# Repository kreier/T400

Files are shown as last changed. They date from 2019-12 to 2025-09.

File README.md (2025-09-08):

# T400





Robot car with WiFi, programmed and controlled by MicroPython. The OLED screen gives information about status, connection and WiFi network to connect to (AP mode).

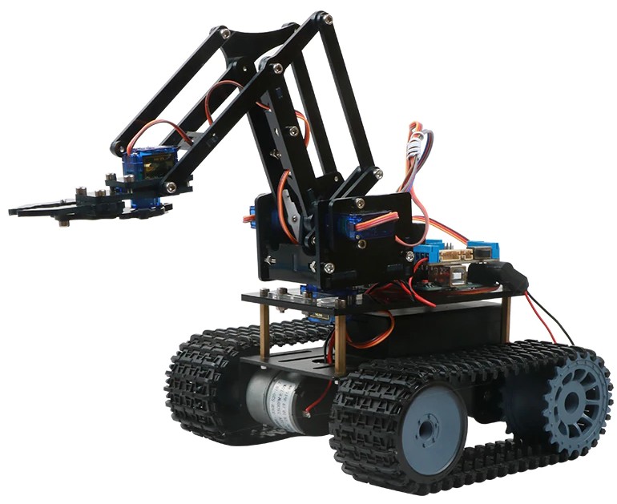
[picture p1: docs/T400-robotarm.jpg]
T400

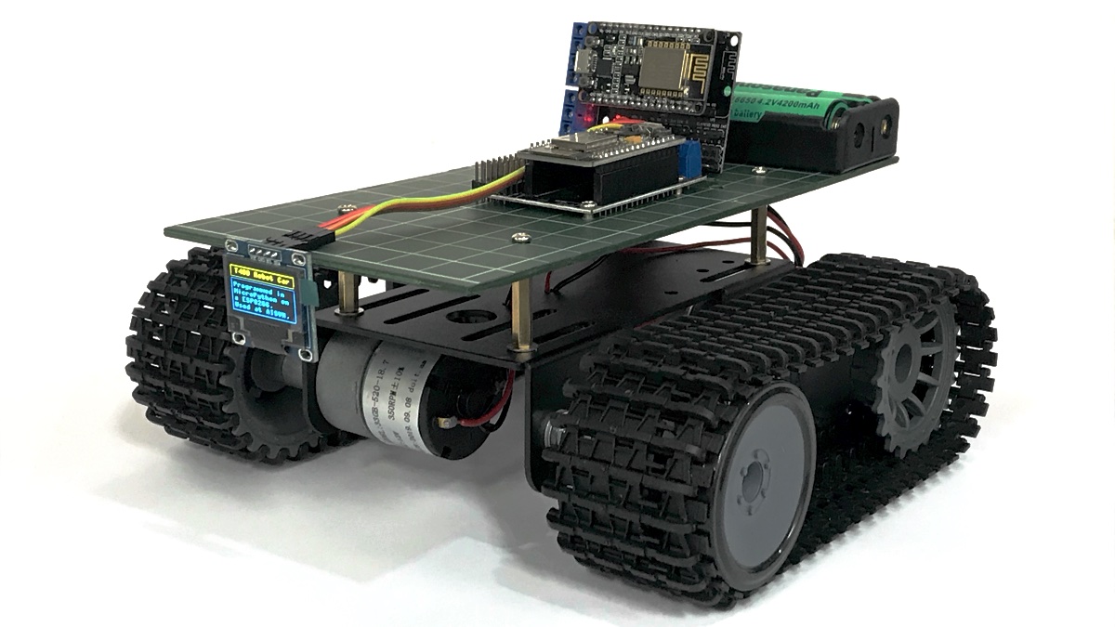
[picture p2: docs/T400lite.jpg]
T400 lite


## Project

This car was build during ASA session III in 2019/2020 at the AISVN. In 11 weeks from February 24th to May 22nd we successfully created 8 robot cars. Here are some pictures of the finished products:

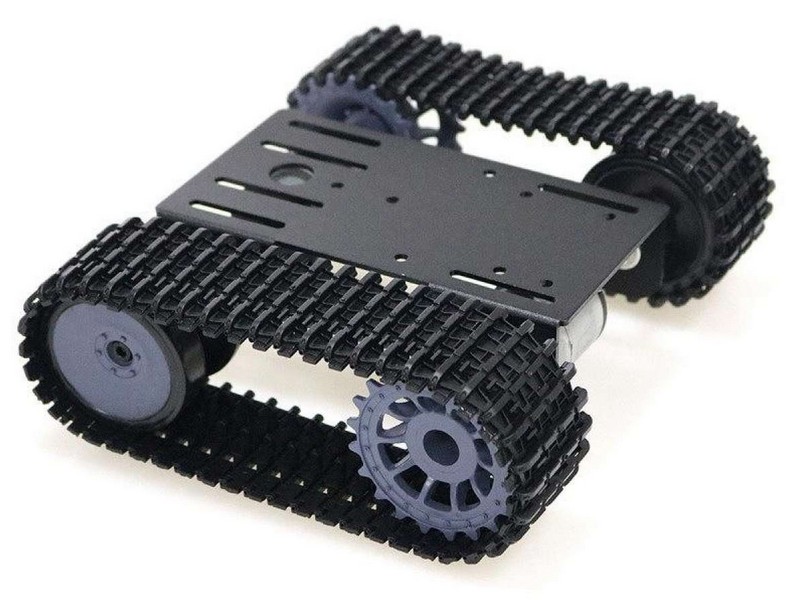
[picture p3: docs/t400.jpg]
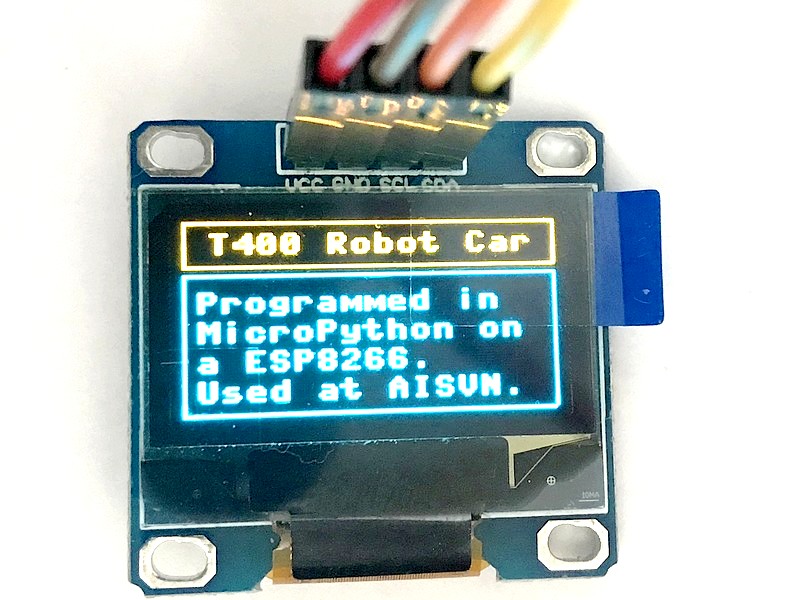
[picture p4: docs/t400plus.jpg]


### Key features

Over the time of 3 months the students will reach different stages of their project, but here are some key features:

- Central unit is a ESP8266 with 32 kByte RAM and 4 GByte Flash memory, running at 160 MHz.
- The programming language is [MicroPython](https://en.wikipedia.org/wiki/MicroPython) with an interactive prompt [REPL](https://en.wikipedia.org/wiki/Read%E2%80%93eval%E2%80%93print_loop).
- The control unit is powered by a standard 5V powerbank.
- The drive unit is a caterpillar base with two 12V motors.
- The robot car can be controlled via WiFi.
- An OLED display 128x64 (ssd1306) gives status updates.

## Materials

The materials used for this project were ordered at [IC ĐÂY RỒI](https://icdayroi.com/), [thegioiic.com](https://thegioiic.com/) and [lazada.vn](https://www.lazada.vn/#). Here is a list of materials:

| Nr | Name | Amount | Unit Price | Sum | Supplier |
|:--:|---|:---:|---:|---:|:---:|
|  1 |ESP8266 NodeMCU | 1 | 83000 VND| 83000 VND| [link thegioiic](https://thegioiic.com/products/lua-esp8266-cp2102-nodemcu-wifi-module) |
| 2 |Motor Shield L293D | 1 | 30000 VND| 30000 VND| [link thegioiic](https://thegioiic.com/products/esp12e-lua-l293d-de-ra-chan-wifi-esp8266-nodemcu) |
| 3 |OLED display 126x64 I2C | 1 | 79000 VND| 79000 VND| [link thegioiic](https://thegioiic.com/products/lcd-oled-0-96inch-128x64-iic-4pin-chu-trang) |
| 4 |Wires DuPont MF and FF | 20 | 300 VND| 6000 VND| [link thegioiic](https://thegioiic.com/products/day-be-cai-cai-dai-15cm) |
| 5 |Robot caterpillar 12V unit | 1 | 483000 VND| 483000 VND| [link lazada.vn](https://www.lazada.vn/products/smart-tank-car-chassis-tracked-caterpillar-crawler-robot-platform-with-dual-dc-12v-motor-for-diy-for-arduino-t101-ptp101-i402162026-s6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) |
| 6 |Powerbank 10000 mAh 2 USB | 1 | 249000 VND| 249000 VND| [link nguyenkim](https://www.nguyenkim.com/pin-sac-du-phong-mili-power-shine-ii-hb-m90bk.html) |
| 7 |DC step-up converter 5V 12V | 1 | 23000 VND| 23000 VND| [link thegioiic](https://thegioiic.com/products/xl6009-mach-tang-ap-4a) |
| 8 |Robot 4DOF kit | 1 | 246000 VND| 246000 VND| [link lazada.vn](https://www.lazada.vn/products/4-dof-acrylic-chua-lap-rap-diy-canh-tay-robot-diy-bo-cho-arduino-may-lam-ho-tro-hoc-tap-sg90-servo-i267650656-s391094259.html) |
| 9 |Servo SG90 | 5 | 29000 VND| 145000 VND| [link icdayroi](https://icdayroi.com/servo-sg90) |
| 10 |Ultrasonic Module US-100 3.3V | 1 | 59000 VND| 59000 VND| [link thegioiic](https://thegioiic.com/products/us-100-module-cam-bien-sieu-am) |
| 11 |I2C servo controller PCA9685 | 1 | 49000 VND| 49000 VND| [link thegioiic](https://thegioiic.com/products/pca9685-dieu-khien-dong-co-servo-12bit-pwm-6-kenh) |
| 12 |USB male connector Type A | 2 | 1800 VND| 3600 VND| [link thegioiic](https://thegioiic.com/products/cong-usb2-0-typea-4pin-dau-duc-han-day) |
| 13 |Buzzer 3.3 Volt | 1 | 3000 VND| 3000 VND| [link thegioiic](https://thegioiic.com/products/module-coi-buzzer-3-3v-5v) |
| 14 |Screw M3 8mm | 8 | 550 VND| 4400 VND| [link thegioiic](https://thegioiic.com/products/vit-pm-m3-x-8mm) |
| 15 |HEX-M3 spacer 15mm | 4 | 1000 VND| 4000 VND| [link thegioiic](https://thegioiic.com/products/tru-dong-hex-m3-cai-cai-dai-15mm) |
|  | |  |  VND| 1467000 VND|  |

## Pin layout

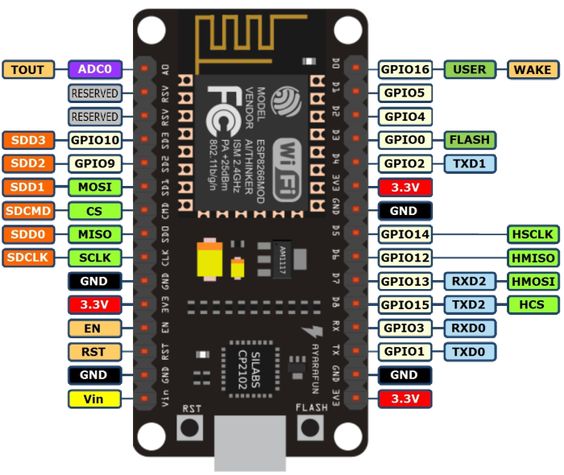
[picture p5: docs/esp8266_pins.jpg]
Pin esp8266


## Code

This is an example of the MicroPython code we are going to use:

``` py
from machine import Pin, I2C
import ssd1306

# ESP32 Pin assignment 
# i2c = I2C(1, scl=Pin(22), sda=Pin(21))

# ESP8266 Pin assignment
i2c = I2C(scl=Pin(12), sda=Pin(14))

oled_width = 128
oled_height = 64
oled = ssd1306.SSD1306_I2C(oled_width, oled_height, i2c)

# draw some boxes

for x in range(0, 127): # horizontal lines
  oled.pixel(x, 0, 1)
  oled.pixel(x, 15, 1)
  oled.pixel(x, 16, 1)
  oled.pixel(x, 63, 1)
  
for y in range(0, 63): # vertical lines
  oled.pixel(0, y, 1)
  oled.pixel(127, y, 1)

oled.text('T400 Robot Car', 8, 4)
oled.text('Programmed in', 4, 22)
oled.text('MicroPython on', 4, 32)
oled.text('a ESP8266.', 4, 42)
oled.text('Used at AISVN.', 4, 52)
  
oled.show()
```

## I2C connector

`2020/07/09`

Following the inspiration of SparkFun with their [QWIIC](https://www.sparkfun.com/qwiic#products) connector I tried to replicate the pin order. But instead of SMD 1.0 mm connector I just use the regular 2.54mm raster with XH connector on the board and respective 4 pin connector wire.

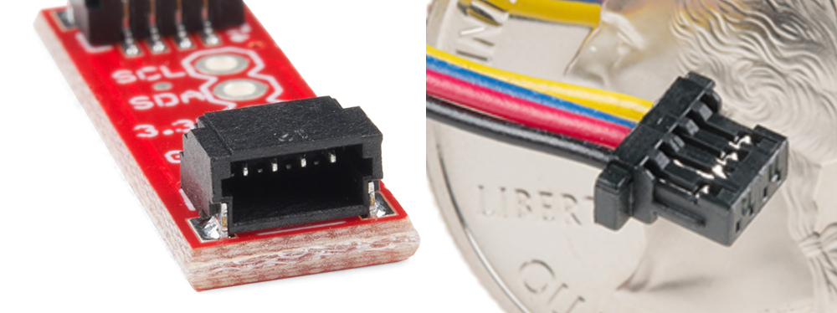
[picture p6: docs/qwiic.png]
QWIIC system


Following the same order the pins are assigned:
1. black - GND
2. red - 3.3 V
3. blue - SDA
4. yellow - SCL

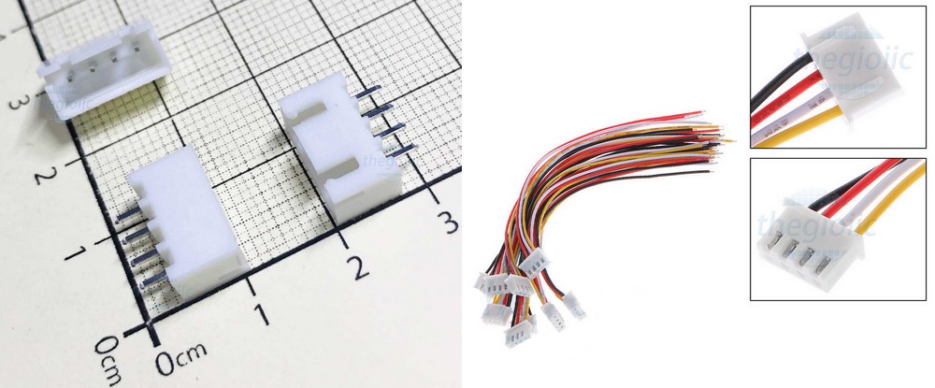
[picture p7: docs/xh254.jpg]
XH 2.54 connector


The order does not match several OLED displays, but the ZS-042 rtc clock, the 1602 display adapter and many more.

`2020/11/27`

With the new [T-Display](https://kreier.github.io/t-display/) project I included the I2C connector as well. The pins look like this:

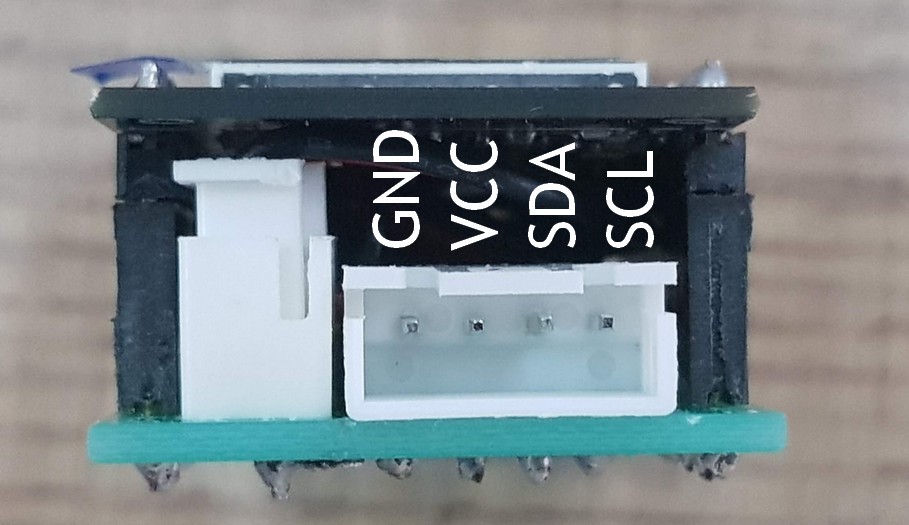
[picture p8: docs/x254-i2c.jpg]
I2C on T-Display


At the ESP32 SCL (SCK) is on GPIO 22 and SDA (SDI) is on GPIO 21.

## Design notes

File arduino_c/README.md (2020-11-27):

# Programming in C with the Arduino IDE

As a parallel development we have some code for the esp8266 on the motorshield board written in C. It helps troubleshooting behaviour and usability of pins, combinations etc.

The board uses the pin D1 to D4 to control tle L293DD motor bridge. The I2C is usually booked on these pins, they have to be remapped therefore.

## I2C Display 1602

It works only with D5 and D6. D7 and D8 throw errors when unconnected to a I2C bus and stop the program when connected. Same is for SD2 and SD3 (GPIO9 and GPIO10). Connection is

| PIN | GPIO | I2C |
|-----|---|-----|
| D6  | 12 | SDA |
| D5  | 14 | SCL |

``` c
#include <LiquidCrystal_I2C.h>
#include <Wire.h>

LiquidCrystal_I2C lcd(0x27, 16, 2);

void setup(){        // usually I2C on D1 and D2, but used for motor driver
  Wire.begin(12,14); // I2C on D6/GPIO12/SDA and D5/GPIO14/SCL
  lcd.init();
  lcd.backlight();
  pinMode(16, OUTPUT);
}

void loop(){
  for(int i = 0; i < 2; i++){
    lcd.setCursor(0, i);
    lcd.print("Hello, World!");
    digitalWrite(16, i);
    delay(500);
    lcd.clear();
  }
}
```
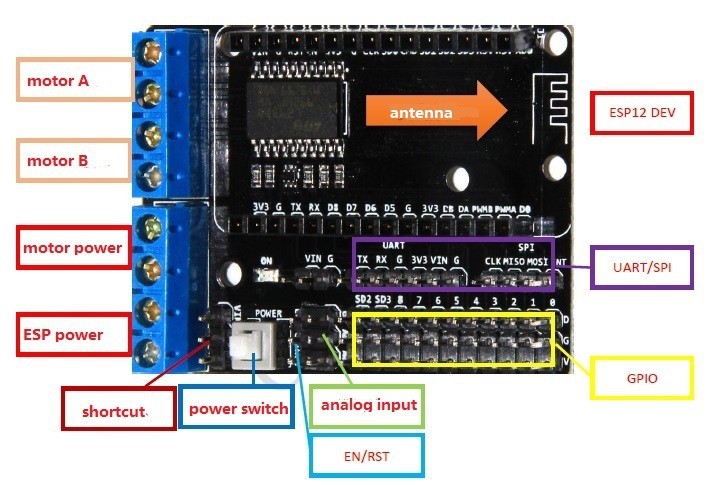
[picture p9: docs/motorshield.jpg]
motorshield


## Remote controlled robot

A great project has been done by [Vincent Lacour](https://github.com/lacour-vincent) to create a remote controlled robot car with an ESP8266. He wrote an app to control the robot using WiFi, let's later update the code to directly control the robot in a browser.

Link to his project (November 2019):

- Code https://github.com/lacour-vincent/wifi-car-esp8266
- Android app: https://play.google.com/store/apps/details?id=com.lacour.vincent.wificaresp8266
- iOS app: not yet there

Other notable projects:

With Remoteme: https://www.hackster.io/WolfxPac/wifi-controlled-robot-using-esp8266-8756b7 2019/01/01

With Blynk: https://www.instructables.com/id/Wifi-Controlled-Robot-Car-Using-Nodemcu-and-Blynk/ 2019/07/05

Simple https://www.hackster.io/alankrantas/simple-nodemcu-wifi-controlled-car-esp8266-c5491e 2019/08/19

## OLED display at I2C

For slightly more money one can get an OLED display for the I2C bus, which has a better resolution than the 1602 display, supports graphics and is smaller in size - perfect for a small robot. To deceide if I should go for 0.96" or 1.3" I ordered both and compared the output of both displays, since both have the same resolution:

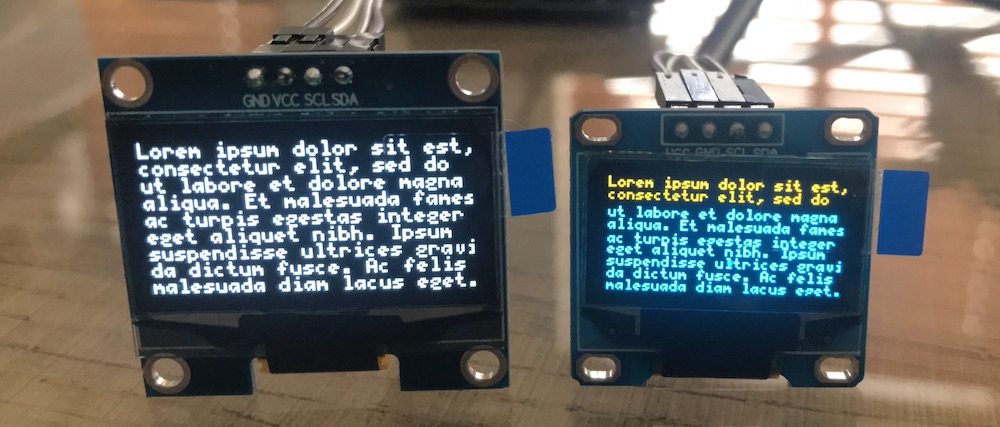
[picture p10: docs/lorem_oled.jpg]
SH1106 and SSD1306


Clearly the larger SH1106 display is to prefer compared to the smaller SSD1306 variant in two colors.

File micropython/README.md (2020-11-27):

# Micropython on the ESP8266

## Install Micropython

Instructions are found at [micropython.org](https://docs.micropython.org/en/latest/esp8266/tutorial/intro.html). For example you can check the size of your flash with `esptool.exe --port COM5 --chip auto flash_id`. Use the firmware found at [the download page of micropython.org](http://micropython.org/download#esp8266) and flash the new firmware with

```
esptool.py --port COM5 --baud 460800 write_flash --flash_size=detect 0 esp8266-20200103-v1.12.bin
```

Now you can connect to your esp8266 using [uPyCraft](http://docs.dfrobot.com/upycraft/) or [Thonny](https://thonny.org/). For the first one you might want to install [SourceCodePro.ttf](https://github.com/kreier/python2018/raw/master/micropython/SourceCodePro.ttf) for all users to avoid the error message.

## Using the OLED display

The OLED display is connected via I2C and the pins are remaped to GPIO 14 (SDA) and GPIO 12 (SCL) because the standard pins are used by the motorshield. In 0.96" and 1.3" it looks like this:

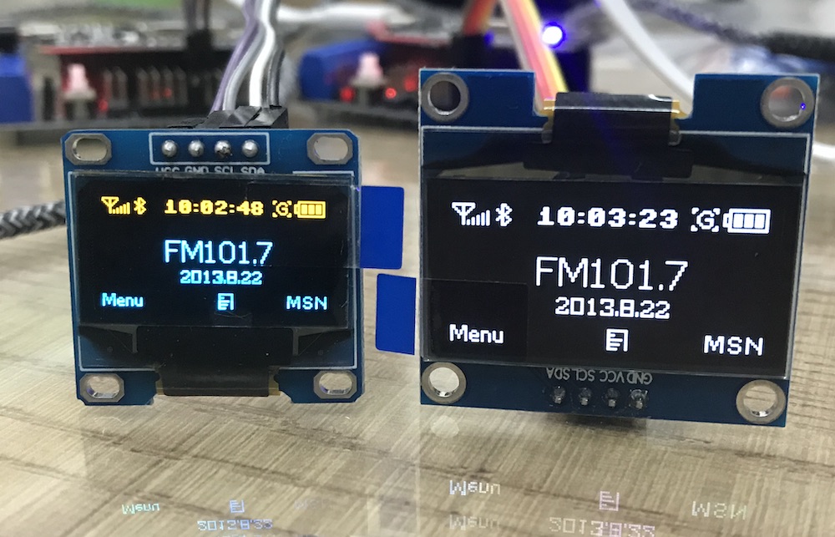
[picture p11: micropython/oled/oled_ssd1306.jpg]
small vs big


## Logfile

`2020/11/27`

Too many external components. The T-Display has a TFT display included, with color and higher resolution and with ESP32 and battery controller ...

`2019/12/05`

Why Micropython? Because we teach python at school. It is used by data scientists. We use it in Jupyter notebooks. It is easier to learn than Arduino C.

And it has REPL - Read Evaluate Print. You get an immediate response. After flashing micropython v1.11 to my NodeMCU in five minutes the first blink from the commandline was working. Flipping pins without compiling and upload a program is GREAT!

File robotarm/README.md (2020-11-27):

# Robotarm

> [Link to robot arm for T400](MeArm/README.md)

The T400 should be equipped with a robot arm. Due to financial constrains we are going to use a $11 (246,000 VND) lasercut acryl 4 DOF arm with SG50 servos. The final robot should look like this:

T400 with robot arm

## 3D printed robot arm - EEZYbotARM MK1 and MK2

In 2015 and italian maker designed a printable [robot arm MK1](https://www.thingiverse.com/thing:1015238). It was very successfull and downloaded more than 120,000 times.

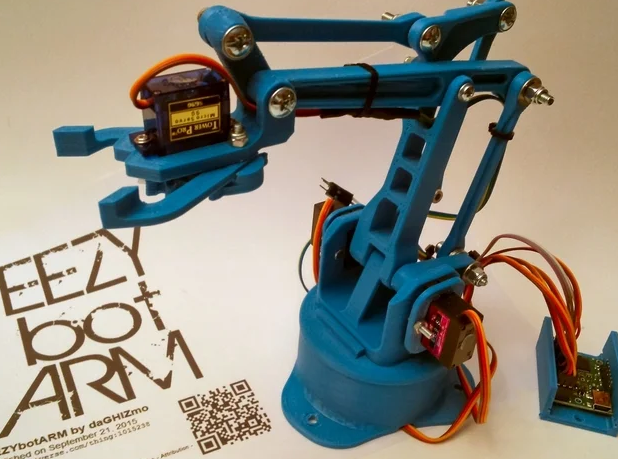
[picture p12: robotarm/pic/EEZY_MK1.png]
EEZYbotARM MK1


Soon he found it to be too small and [created the MK2](https://www.thingiverse.com/thing:1454048) in 2016. It is downloaded at [thingiverse](https://thingiverse.vom) some 110,000 times. You can get it printed in HCMC for example at [makerstore.vn](http://makerstore.vn) for 281,00 VND (MK1) or 525,000 VND (MK2). They have the screws and servos as well.

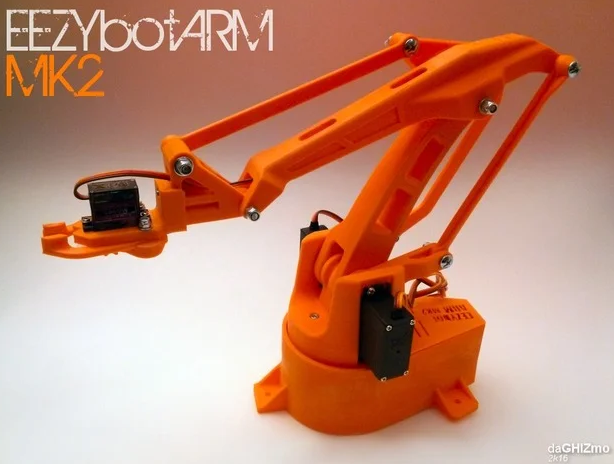
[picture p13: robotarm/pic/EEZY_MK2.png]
EEZYbotARM MK2


## Robot arm 6 DOF from China

At Aliexpress you can order the metal materials for a 6 DOF robot arm for $25. Equipped with 1Nm digital servos like MG996R the product is rather versatile. See it here in action:

`2020/01/12` The kit was just ordered. And we need the servos ...

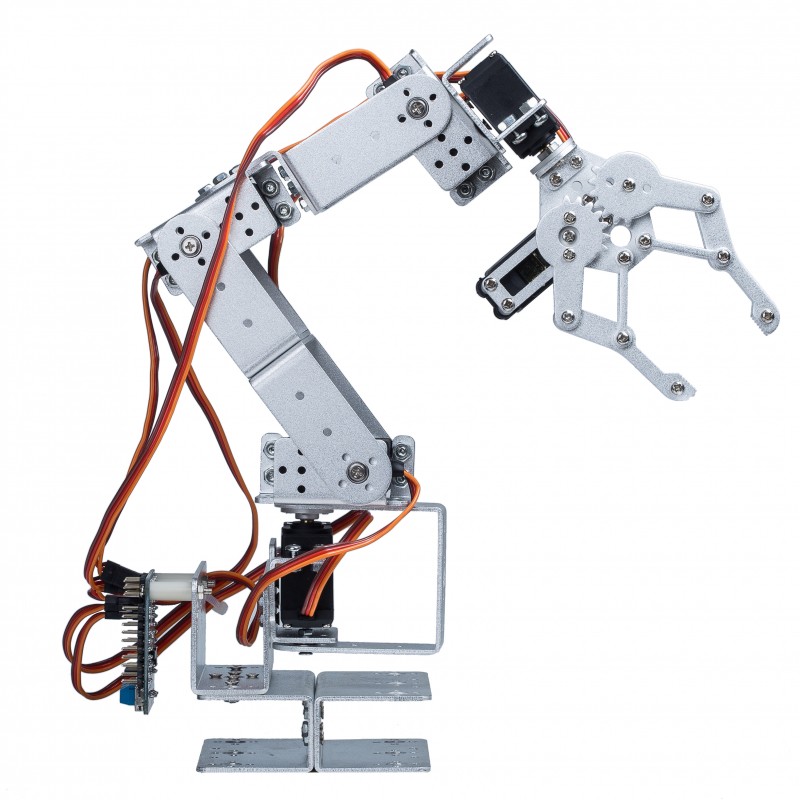
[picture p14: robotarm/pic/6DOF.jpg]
6 DOF


## Design a robot arm ourselves

Inspired by the relative stability of the digital servo driven robot arm and the design of the KUKA KR 3 AGILUS.

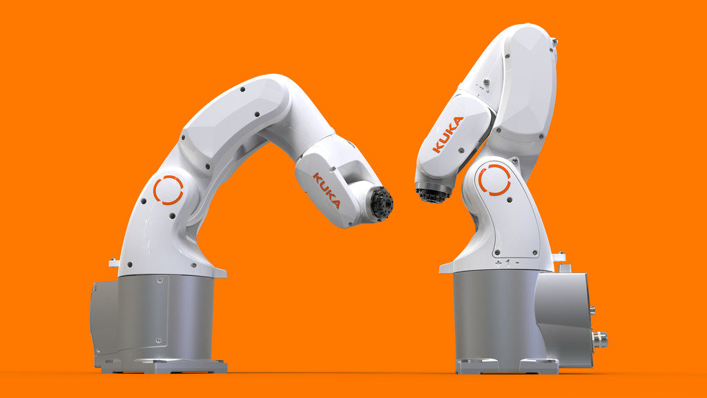
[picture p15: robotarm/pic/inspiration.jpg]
KUKA R3


## Stepper motors

One design with stepper motors is the [WE-R2.4 robot](https://www.thingiverse.com/thing:3327968) that was published in January 2019 by [LoboCNC](https://www.thingiverse.com/LoboCNC/about). Another user [John Lauer](https://github.com/chilipeppr) from [Chilipeppr](http://chilipeppr.com/arm) tried to build this arm and published a [first video](https://www.youtube.com/watch?v=tEbJV32GyYU) in February 2019. [Part 2](https://www.youtube.com/watch?v=RdmdFIhCo4M) from March 2019 had the controller software and hardware based on the ESP32 finishd. But there are several problems:

- Heat
- Homing
- Backlash
- Wiring
- Jogging
- Training

By September 2019 these where addressed and resolved or improved. See [Part 3 video](https://www.youtube.com/watch?v=4o3d7_WZ_DQ). Couldn't find a number for the produced torque or maximum rpm, though.

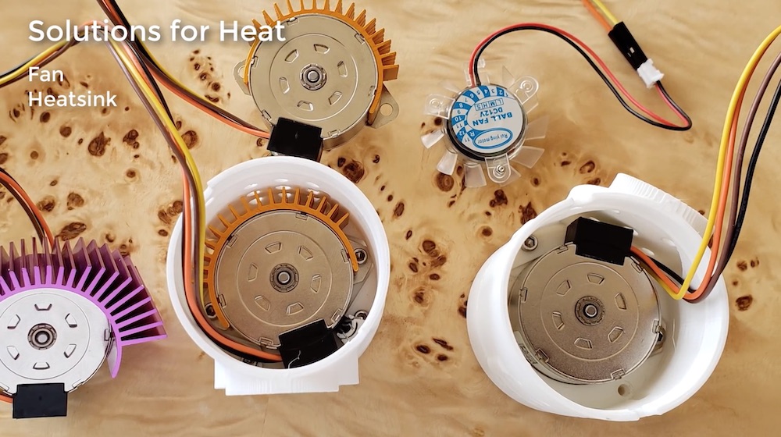
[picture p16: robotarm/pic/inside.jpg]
cooling

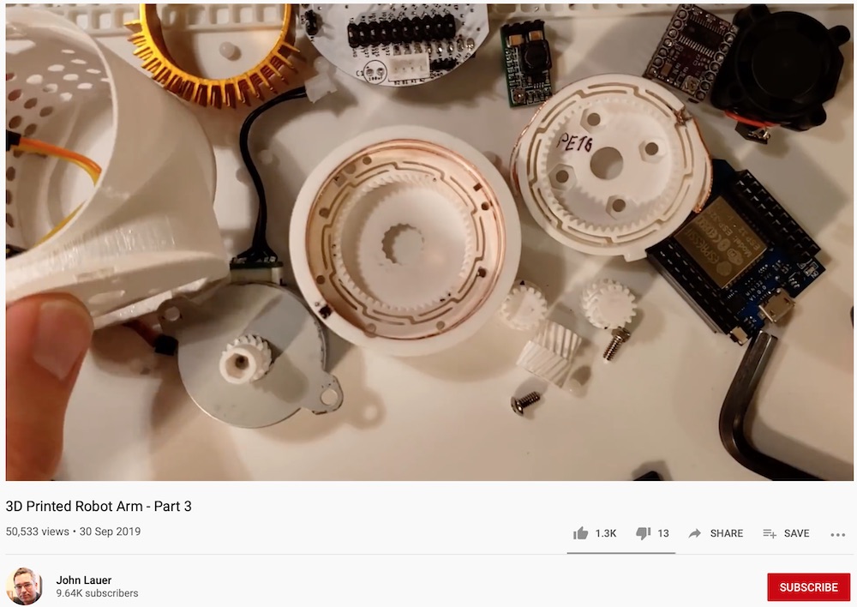
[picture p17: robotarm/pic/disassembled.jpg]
disassembled


## Mirobot - successful Kickstarter from September 2019, starting $295

Project [on Kickstarter](https://www.kickstarter.com/projects/mirobot/mirobot-6-axis-mini-industrial-robot-arm/description). Shipping started January 2020. Got more than $300.000. Later on [Indogogo](https://www.indiegogo.com/projects/mirobot-6-axis-desktop-robot-arm#/) as well. This is how it looks:

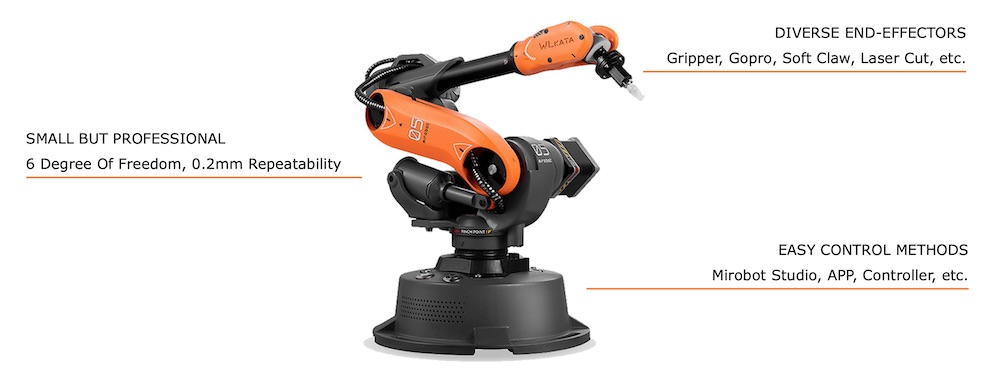
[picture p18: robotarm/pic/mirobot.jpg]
Mirobot


## GLUON by INNFOS - suspended on kickstarter

What [a promising project](https://www.kickstarter.com/projects/1383636492/the-smallest-servomotor-robotic-arm)! Fast and silent brushless actuators for $99 each (SCA QDD Lite-NE30-36) or an entire 4DOF for $519 or 6DOF robot arm for $899. But there might be some tentions with the investors, after funding from 612 backers for $519.848 in November 2019 (success in 30 seconds) the project was suspended by kickstarter in 2020. [Link to video](https://www.youtube.com/watch?v=-xzvWhRDGDU). Looked like this:

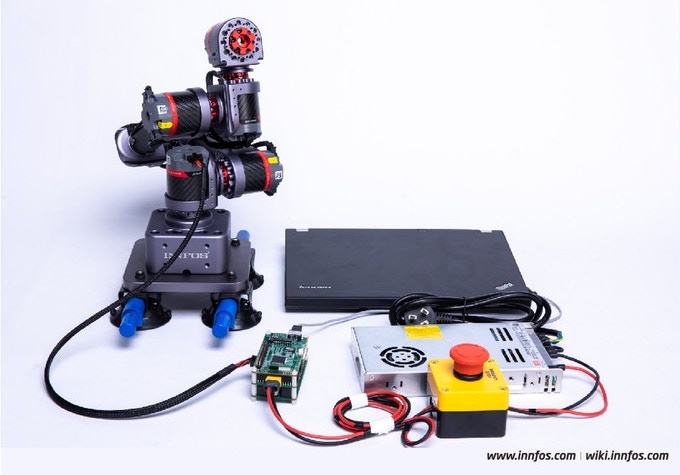
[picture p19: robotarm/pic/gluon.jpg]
INNFOS GLUON


## How to Mechatronics - back to simpler parts

While investigating I found another project that shares a lot of files and information and has a simple robot arm design with servos. It is [this project on howtomechatronics.com](https://howtomechatronics.com/projects/arduino-robot-arm-and-mecanum-wheels-platform-automatic-operation/) from [Dejan](https://howtomechatronics.com/author/howtom12_wp/). He made [a video about his project](https://youtu.be/LBNRGBY5zN8).

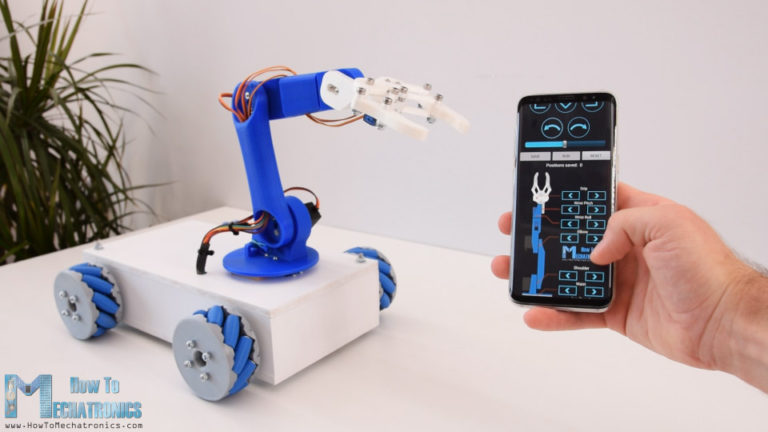
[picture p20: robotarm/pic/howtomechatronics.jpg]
Finished robot


He even created a Android App with MIT App invenbor to control his robot. We might use this for our T400. We don't have the stepper motors for our base as he does, but we might modifiy our code to fit the esp8266 instead of a Arduino Mega.

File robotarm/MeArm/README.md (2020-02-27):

# Robot arm at T400

Limited time and resources led to the decision to use the MeArm v3.0 for our T400 project during ASA3. The assembly should take 25 minutes and can be followed [in this video](https://youtu.be/sPdbs9b5udQ).

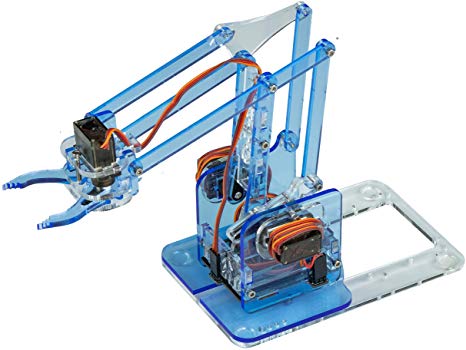
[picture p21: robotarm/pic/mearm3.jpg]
MeArm v3.0


The files are located in this folder and sourced from [here](https://www.thingiverse.com/thing:3420797/files) and [here](https://github.com/mimeindustries/MeArm). The modification is the removal of the text for the lasercutting and shortend of some corners to fit on the base of the robot.

## PCB

The files for the PCB are not provided, so they have to be recreated. This file should serve as inspiration, the rations are all given in the dxf file or can be measured there:

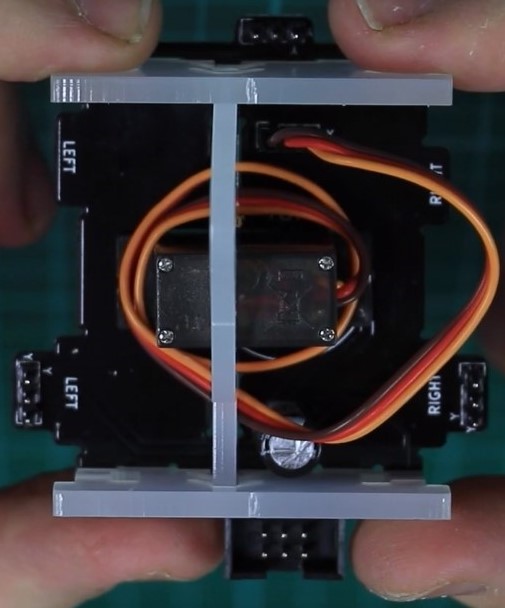
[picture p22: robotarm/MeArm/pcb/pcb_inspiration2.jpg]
PCB closeup


## Additional materials

Aside from the laser cut 3mm acrylic we need some M2.5 screws, no nuts! That's said [here in the video](https://youtu.be/sPdbs9b5udQ?t=455). So I count:

- 16x - M2.5 x 6mm
- 18x - M2.5 x 10mm
- 2x  - M2.5 x 16mm

I'll give it a try on January 31st, 2020.

## Licence

User phenoptix (Ben Gray from Nottingham) from Mime industries/MeArm published the following information on his website regarding the licence:

The hardware is released under [Creative Commons Share-alike 3.0](https://creativecommons.org/licenses/by-sa/3.0/).

All other code is open source so please feel free to do anything you want with it; you buy me a beer if you use this and we meet someday (Beerware license). Also this boiler plate is yoinked from Sparkfun with thanks. Images are CC-SA-NC soz, have the files and design but take your own pics ;)

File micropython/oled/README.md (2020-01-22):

# Text and graphics on 128x64 OLED i2c display

We use pin D5 (GPIO14) as SDA and D6 (GPIO12) as SCL for the i2c bus. The driver library 1306.py should be installed on the device. You can show any image 128x64 monochrome image. For example:

 

The code used is [splash3.py](splash3.py).

## Size 0.96 inch or 1.3 inch

For comparison I ordered the slightly larger display with 1.3 inch as well. It needs the different sh1106 driver, but has the same functions as the ssd1306. Text is easier to read. Here an image:

small vs big

## Convert images

I use the online [tool from majer.ch](http://www.majer.ch/lcd/adf_bitmap.php) and convert the code from ', 0x87' to '\x87' in the bytearray. Follow this instructions:

To create an image there is a description at [the micropython forum](https://forum.micropython.org/viewtopic.php?t=2974). In short deshipu says:

The buffer in the previous exampe is created by scanning the original image pixel-by-pixel and setting the bits of the bytes depending on whether they are supposed to be on or off. The alignment of the bytes is as follows (example of a 16x16 image, the digits signify the bits of each byte):

```
a7 b7 c7 d7 e7 f7 g7 h7 i7 j7 k7 l7 m7 n7 o7 p7
a6 b6 c6 d6 e6 f6 g6 h6 i6 j6 k6 l6 m6 n6 o6 p6
a5 b5 c5 d5 e5 f5 g5 h5 i5 j5 k5 l5 m5 n5 o5 p5
a4 b4 c4 d4 e4 f4 g4 h4 i4 j4 k4 l4 m4 n4 o4 p4
a3 b3 c3 d3 e3 f3 g3 h3 i3 j3 k3 l3 m3 n3 o3 p3
a2 b2 c2 d2 e2 f2 g2 h2 i2 j2 k2 l2 m2 n2 o2 p2
a1 b1 c1 d1 e1 f1 g1 h1 i1 j1 k1 l1 m1 n1 o1 p1
a0 b0 c0 d0 e0 f0 g0 h0 i0 j0 k0 l0 m0 n0 o0 p0
q7 r7 s7 t7 u7 v7 w7 x7 y7 z7 A7 B7 C7 D7 E7 F7
q6 r6 s6 t6 u6 v6 w6 x6 y6 z6 A6 B6 C6 D6 E6 F6
q5 r5 s5 t5 u5 v5 w5 x5 y5 z5 A5 B5 C5 D5 E5 F5
q4 r4 s4 t4 u4 v4 w4 x4 y4 z4 A4 B4 C4 D4 E4 F4
q3 r3 s3 t3 u3 v3 w3 x3 y3 z3 A3 B3 C3 D3 E3 F3
q2 r2 s2 t2 u2 v2 w2 x2 y2 z2 A2 B2 C2 D2 E2 F2
q1 r1 s1 t1 u1 v1 w1 x1 y1 z1 A1 B1 C1 D1 E1 F1
q0 r0 s0 t0 u0 v0 w0 x0 y0 z0 A0 B0 C0 D0 E0 F0
```

I used the following code to generate it:

``` py
import pygame

image = pygame.image.load("1bit-logo.png")
buffer = bytearray((image.get_height() // 8) * image.get_width())
i = 0
for y in range(image.get_height() // 8):
    for x in range(image.get_width()):
        byte = 0
        for bit in range(8):
            pixel = image.get_at((x, y * 8 + bit))
            if pixel[0] != 255:
                byte |= (1 << bit)
        buffer[i] = byte
        i += 1
print(repr(buffer))
```

After that _kamikaze_ added: `or you could use ImageMagick's convert and store it in file to save RAM`

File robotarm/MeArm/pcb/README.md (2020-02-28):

# PCB for MeArm3

The MeArm 3.0 uses a custom PCB to connect the 4 servos to a single flat cable with 6 pins and provide a physical base plate for the ground servo at the same time.

From the assemble video you can guess the shape:

PCB closeup

Since the shematics is not provided, it has to be recreated in EAGLE. Here my attempts: 

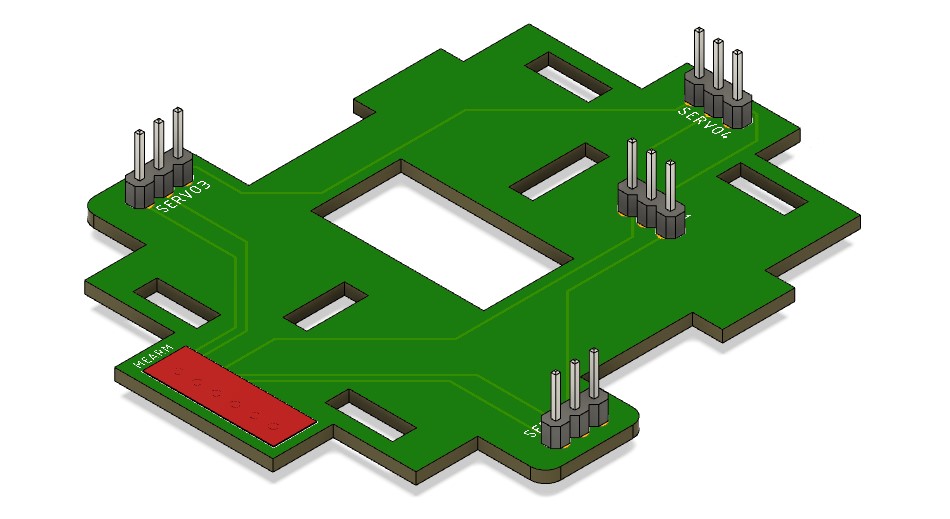
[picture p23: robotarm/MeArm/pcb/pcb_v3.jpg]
PCB v3


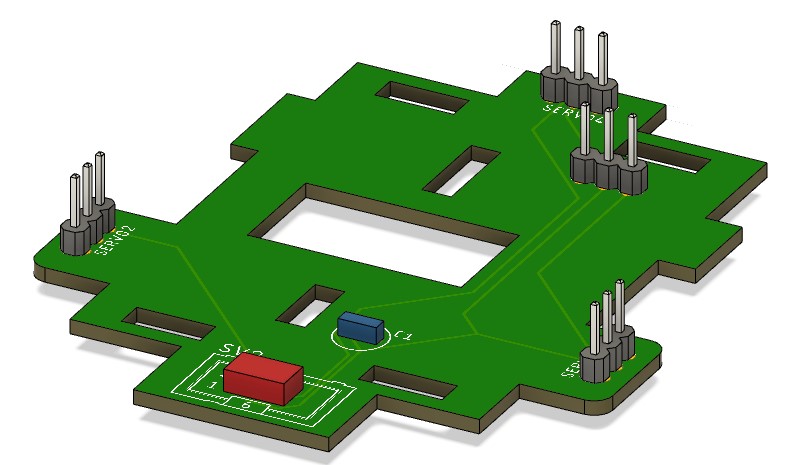
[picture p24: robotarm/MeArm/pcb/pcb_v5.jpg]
PCB v5


MeArm v3.0

The files are located in this folder and sourced from [here](https://www.thingiverse.com/thing:3420797/files) and [here](https://github.com/mimeindustries/MeArm). The modification is the removal of the text for the lasercutting and shortend of some corners to fit on the base of the robot.

## PCB

The files for the PCB are not provided, so they have to be recreated. This file should serve as inspiration, the rations are all given in the dxf file or can be measured there:

PCB closeup

## Additional materials

Aside from the laser cut 3mm acrylic we need some M2.5 screws, no nuts! That's said [here in the video](https://youtu.be/sPdbs9b5udQ?t=455). So I count:

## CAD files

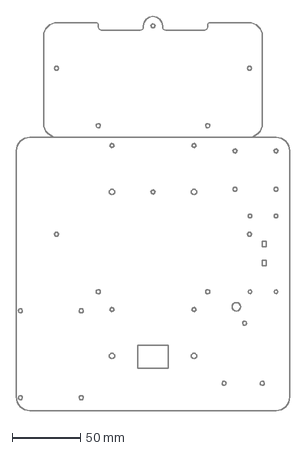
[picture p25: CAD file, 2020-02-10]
platform/T400platform.dxf
200.0 x 288.5 mm

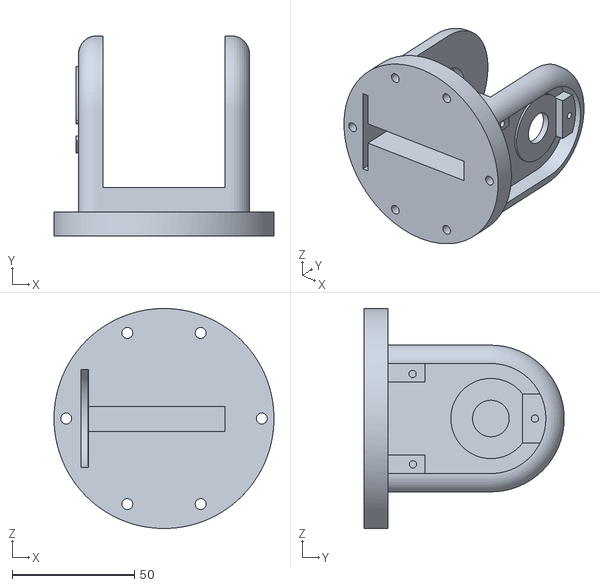
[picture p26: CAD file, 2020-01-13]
robotarm/base2.stl
90.0 x 82.0 x 90.0

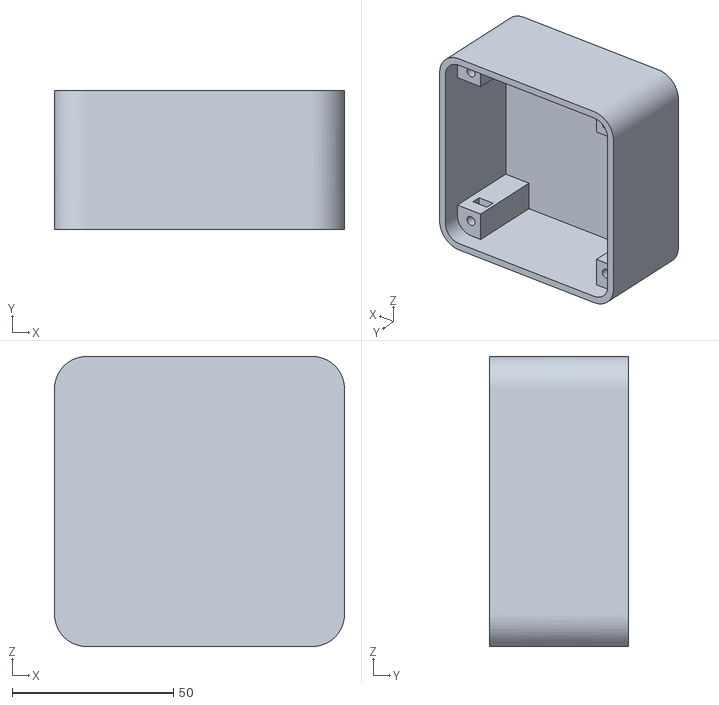
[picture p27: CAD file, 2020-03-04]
robotarm/loudspeaker/Box9.stl
90.0 x 43.0 x 90.0

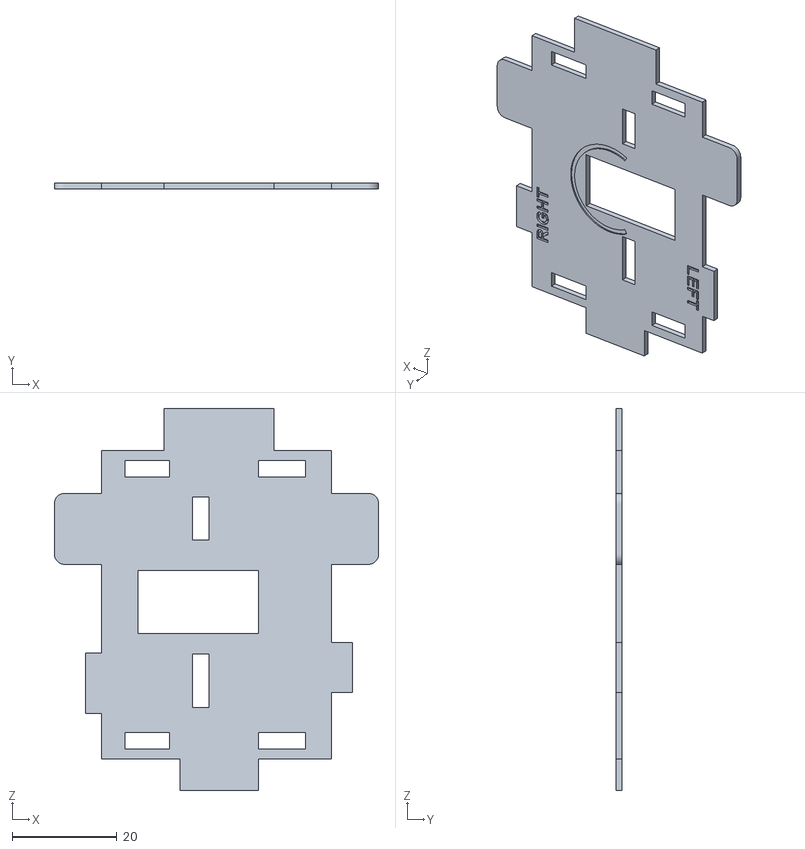
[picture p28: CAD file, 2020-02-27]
robotarm/MeArm/pcb/pcb_base v3.stl
62.0 x 1.20 x 73.0

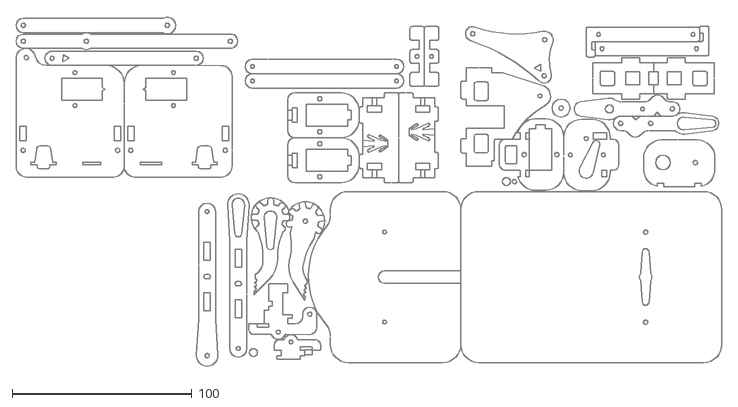
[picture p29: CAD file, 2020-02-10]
robotarm/MeArm/T400arm_plain.dxf
392.1 x 194.9

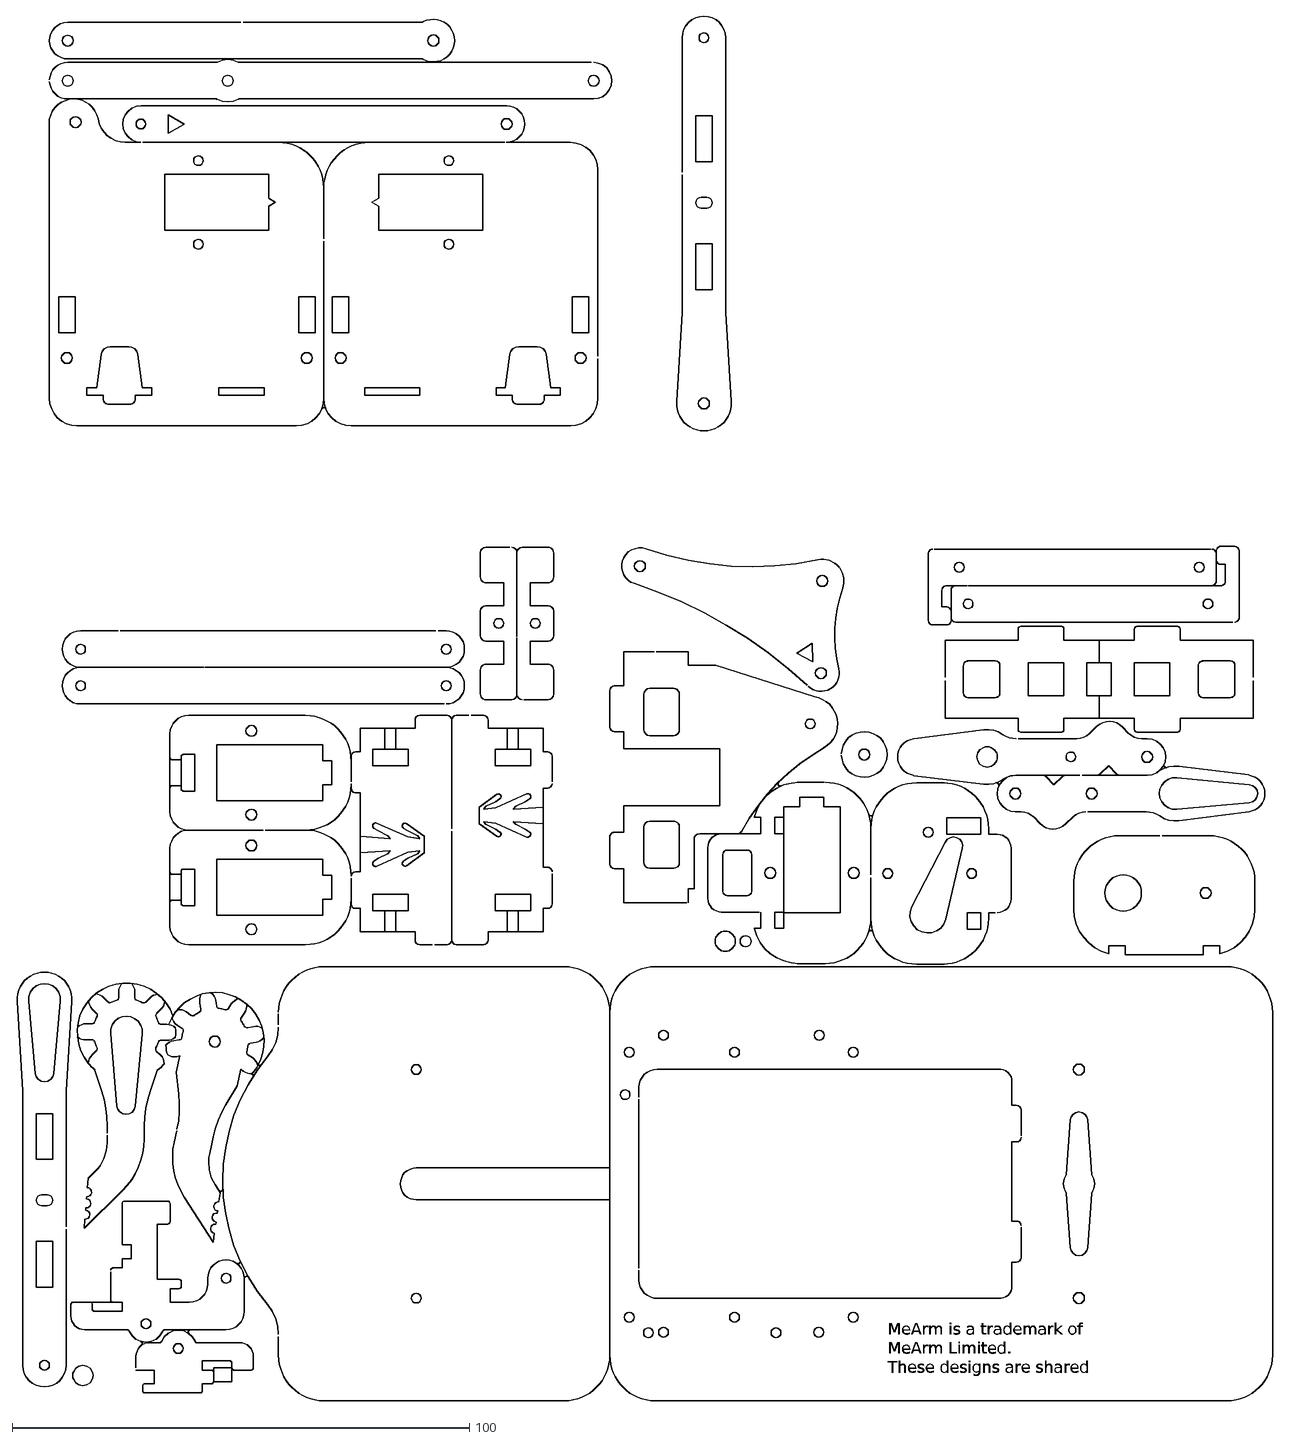
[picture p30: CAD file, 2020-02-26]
robotarm/MeArm/v3.0/MeArm3.0modified.dxf
MeArm is a trademark of
MeArm Limited.
These designs are shared

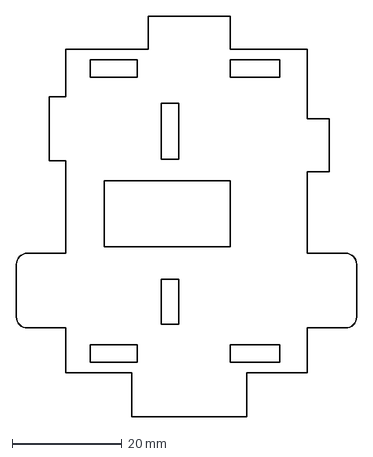
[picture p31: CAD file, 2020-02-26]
robotarm/MeArm/pcb/pcb_base_v4.dxf
62.0 x 73.0 mm

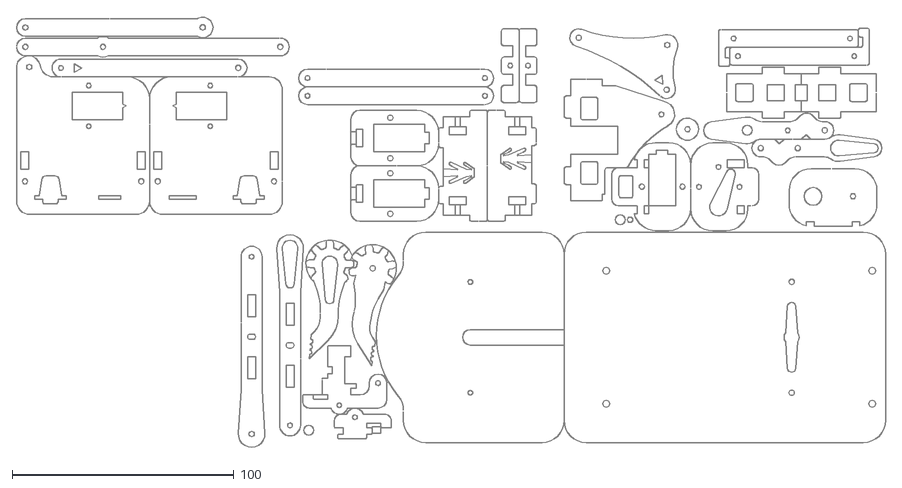
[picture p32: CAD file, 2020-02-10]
robotarm/MeArm/T400arm.dxf
392.1 x 194.9

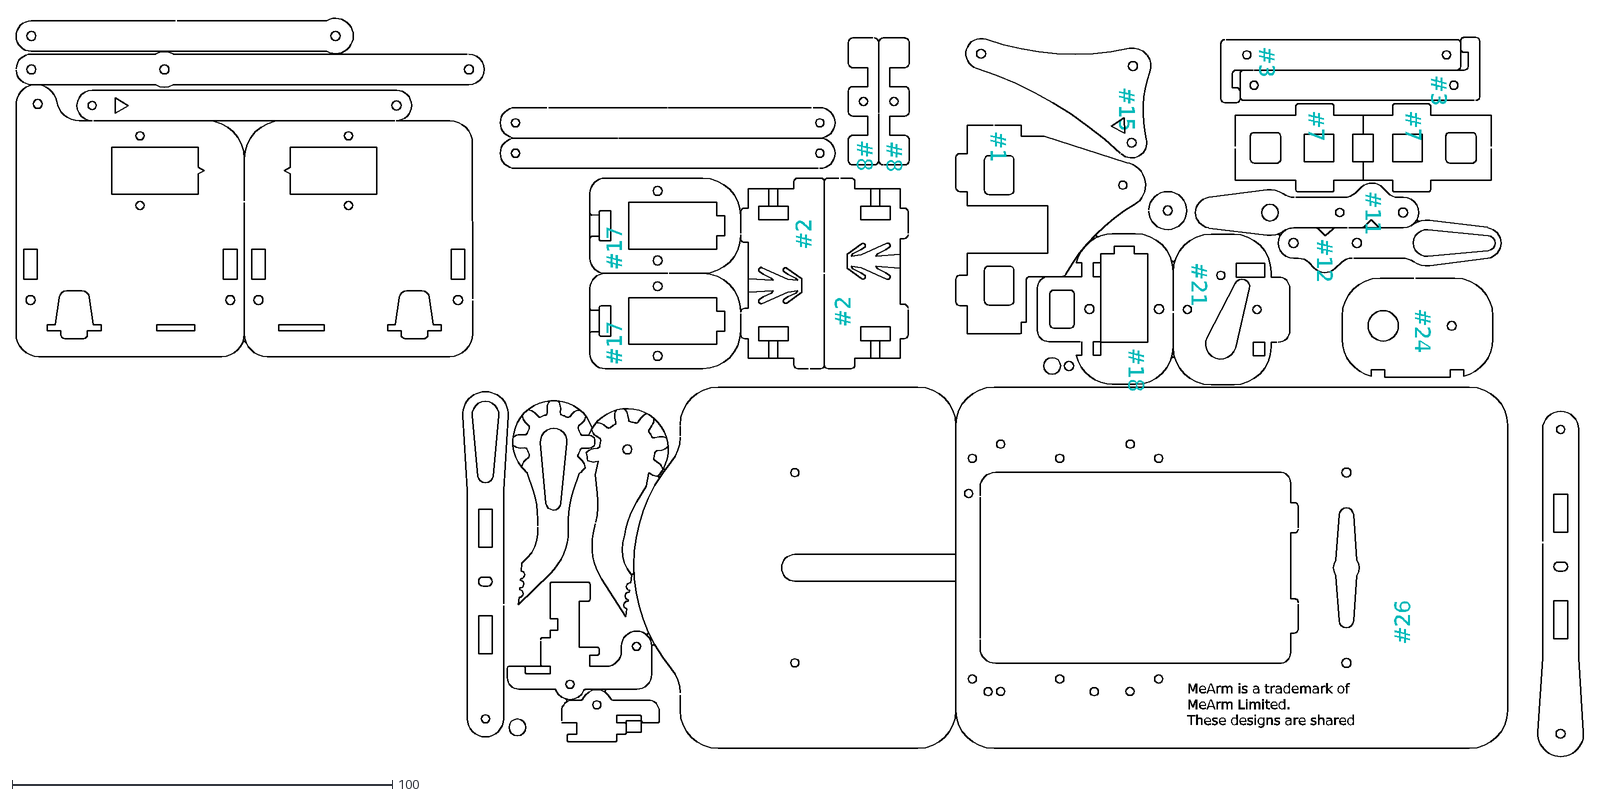
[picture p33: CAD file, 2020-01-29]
robotarm/MeArm/v3.0/MeArm3.0.dxf
#26
#1
#3
#7
#8
#11
#12
#15
#18
#21
#24
#2
#17
MeArm is a trademark of
MeArm Limited.
These designs are shared

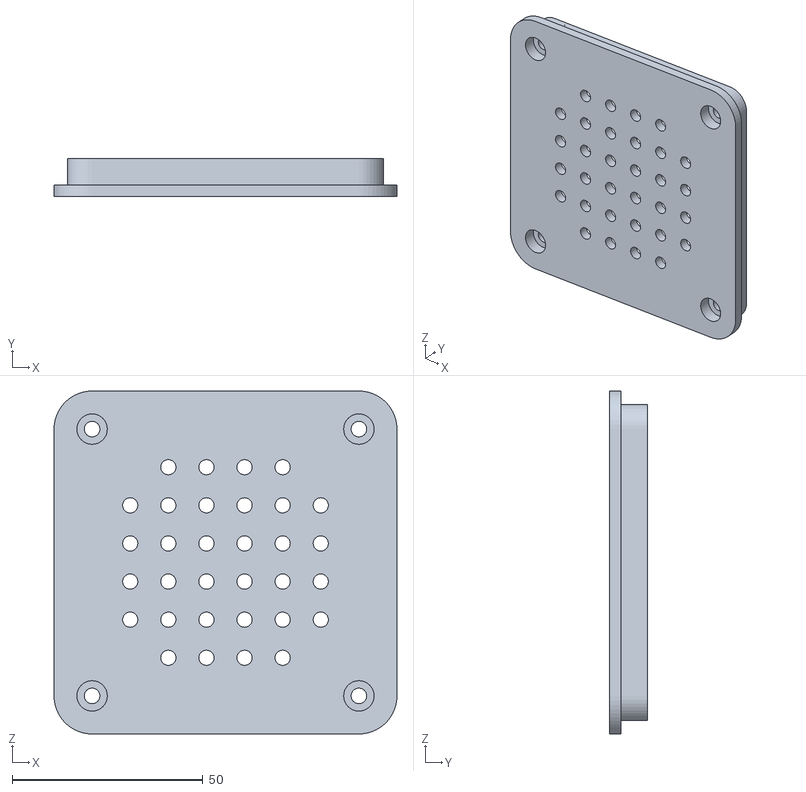
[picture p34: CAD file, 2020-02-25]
robotarm/loudspeaker/Base9.stl
90.0 x 10.0 x 90.0

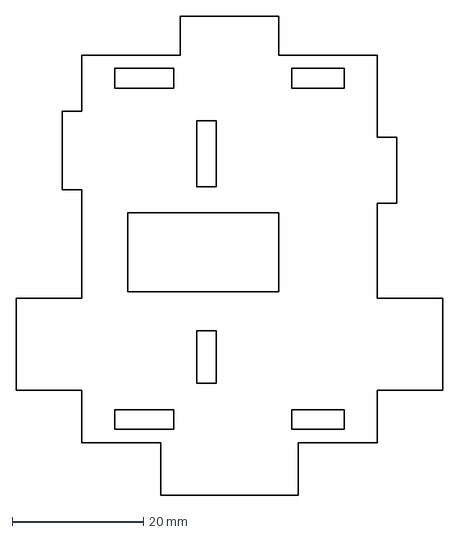
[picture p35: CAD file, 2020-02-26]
robotarm/MeArm/pcb/pcb_base.dxf
65.0 x 73.0 mm

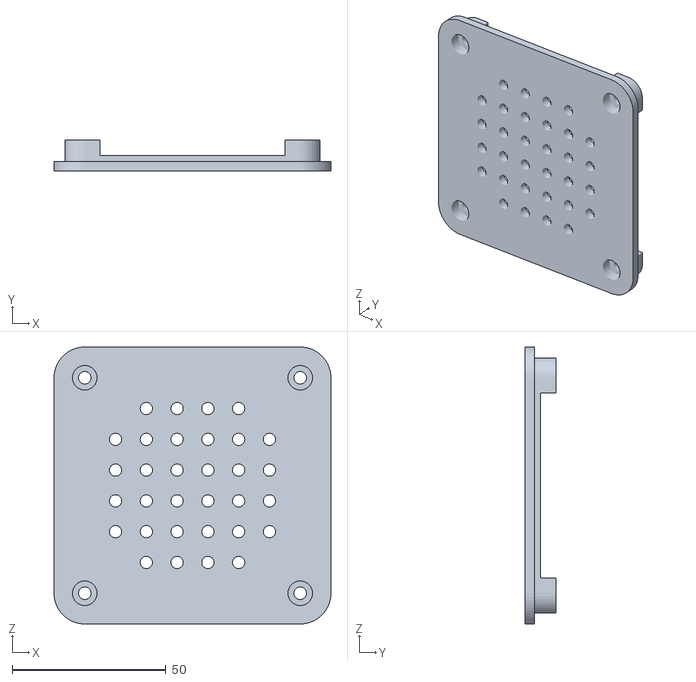
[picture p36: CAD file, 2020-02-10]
robotarm/loudspeaker/Base 9 simple v3.stl
90.0 x 10.0 x 90.0

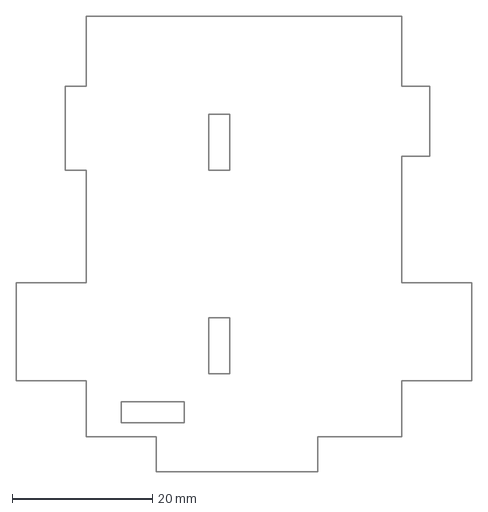
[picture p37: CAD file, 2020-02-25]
robotarm/MeArm/pcb/PCB_shape.dxf
65.0 x 65.0 mm

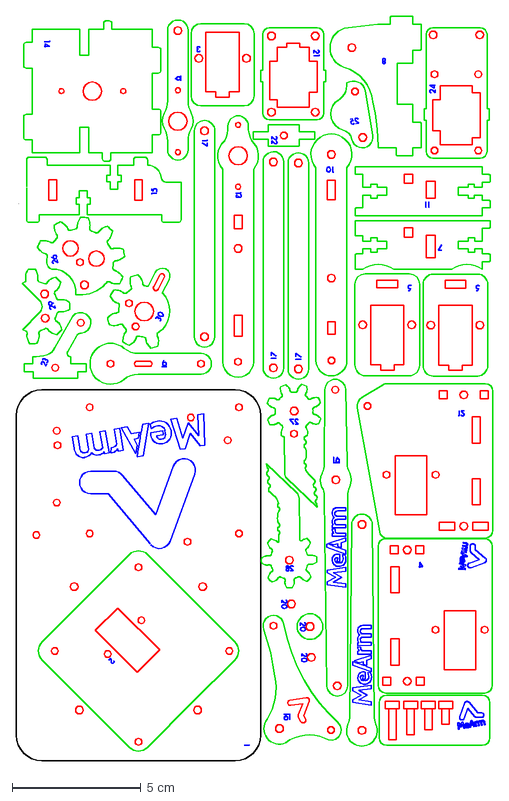
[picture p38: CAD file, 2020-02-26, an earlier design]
robotarm/MeArm/v1.1/MeArm1.1modified.dxf
18.5 x 28.9 cm

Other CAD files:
robotarm/loudspeaker/Box 9 simple v4.stl
robotarm/MeArm/pcb/pcb_base_flipped v2.dxf
robotarm/MeArm/v1.1/MeArm1.1.dxf
robotarm/loudspeaker/Box 9 simple v2.stl
robotarm/MeArm/pcb/pcb_base v2.dwg
robotarm/MeArm/pcb/pcb_base v2.dxf
robotarm/MeArm/pcb/pcb_base v2.stl
robotarm/MeArm/pcb/pcb_base_v3.dxf
robotarm/MeArm/v1.1/MeArm1.1modified.dwg
robotarm/MeArm/v3.0/MeArm3.0modified.dwg

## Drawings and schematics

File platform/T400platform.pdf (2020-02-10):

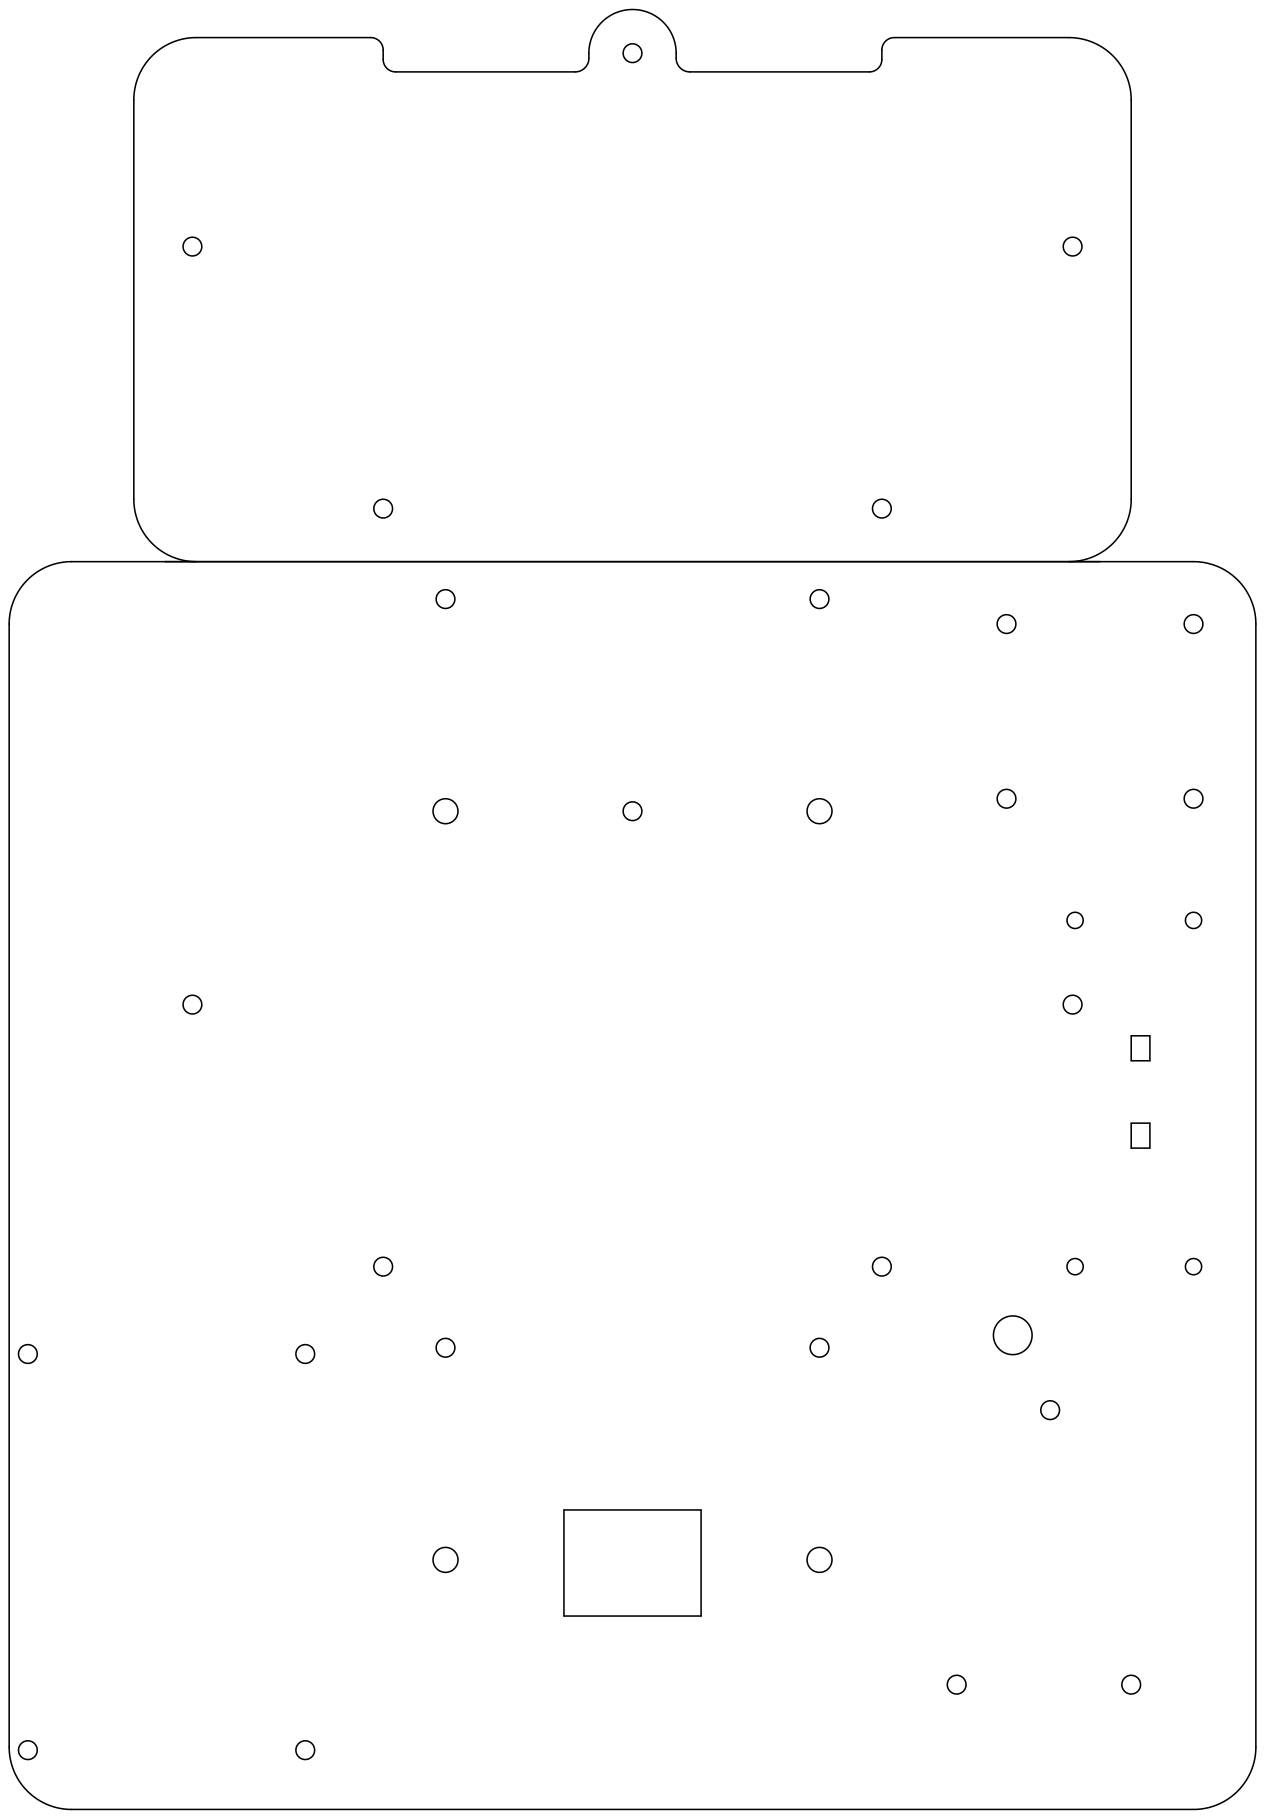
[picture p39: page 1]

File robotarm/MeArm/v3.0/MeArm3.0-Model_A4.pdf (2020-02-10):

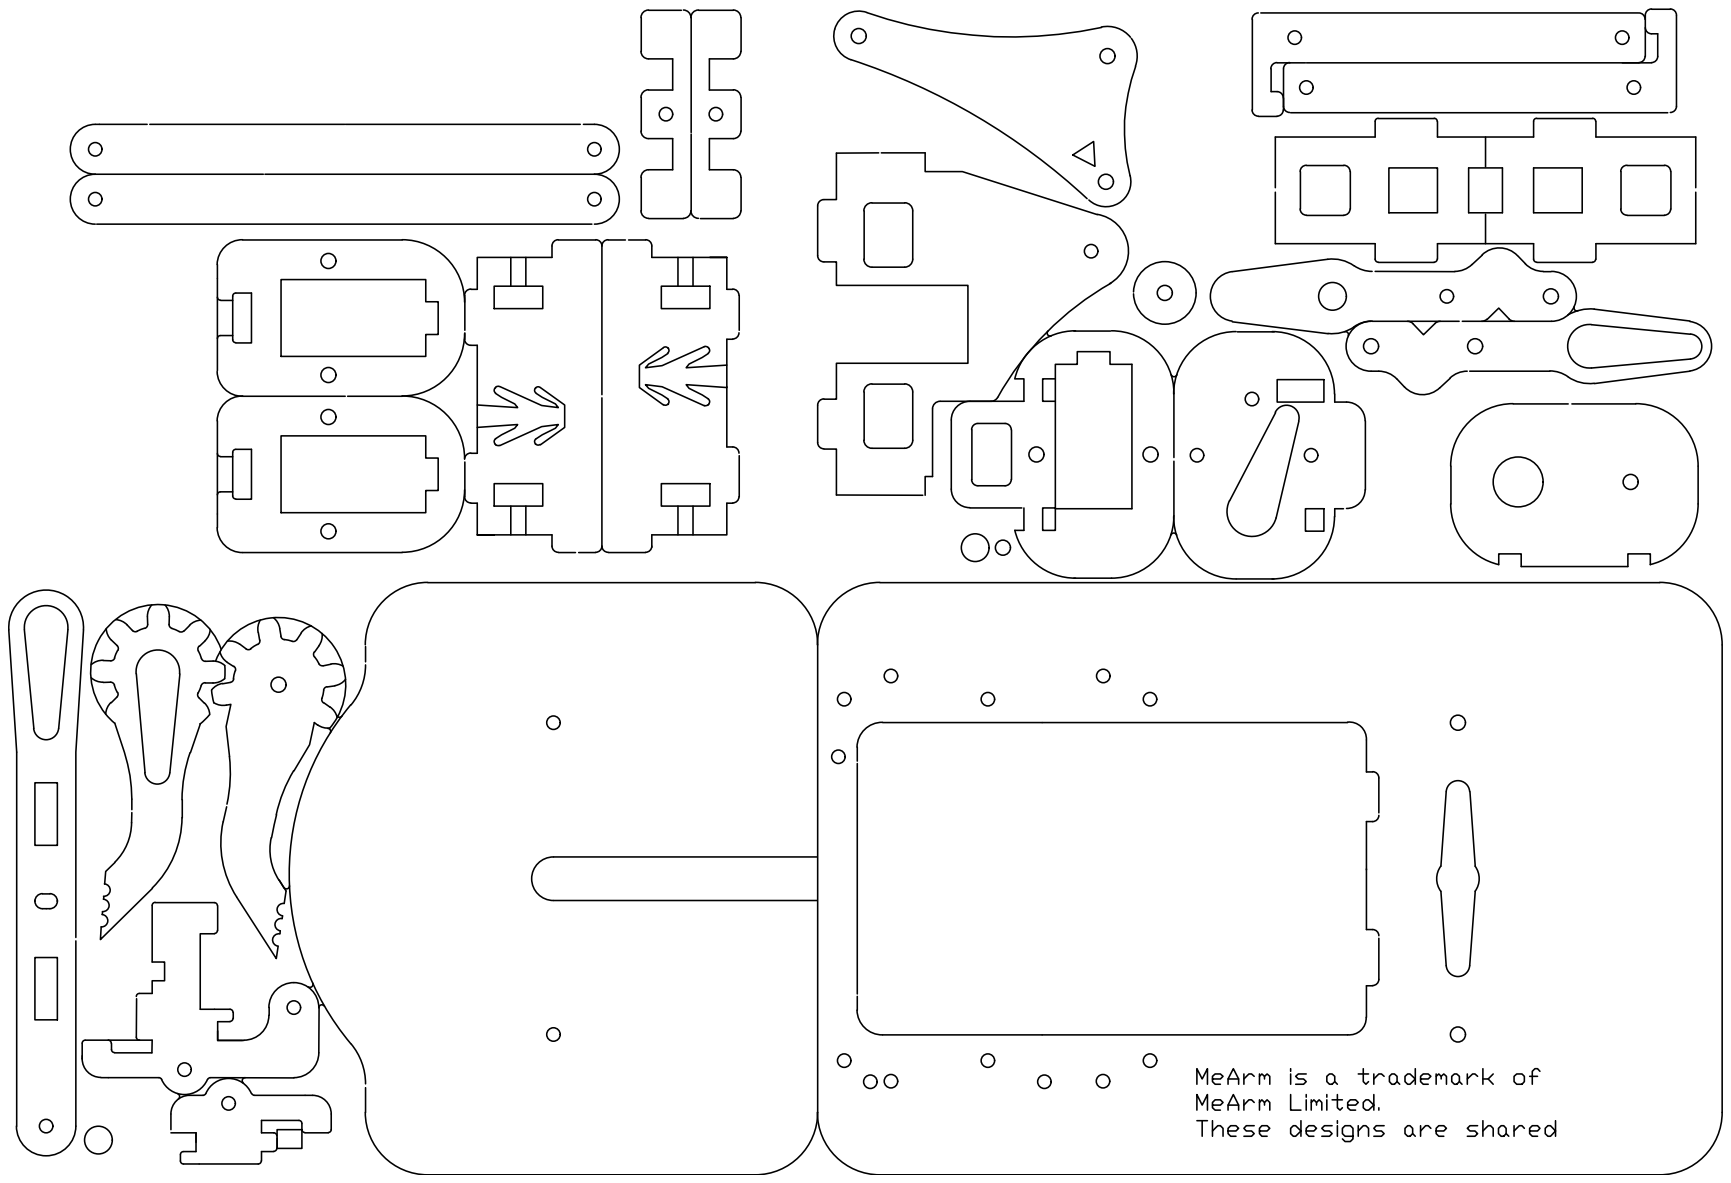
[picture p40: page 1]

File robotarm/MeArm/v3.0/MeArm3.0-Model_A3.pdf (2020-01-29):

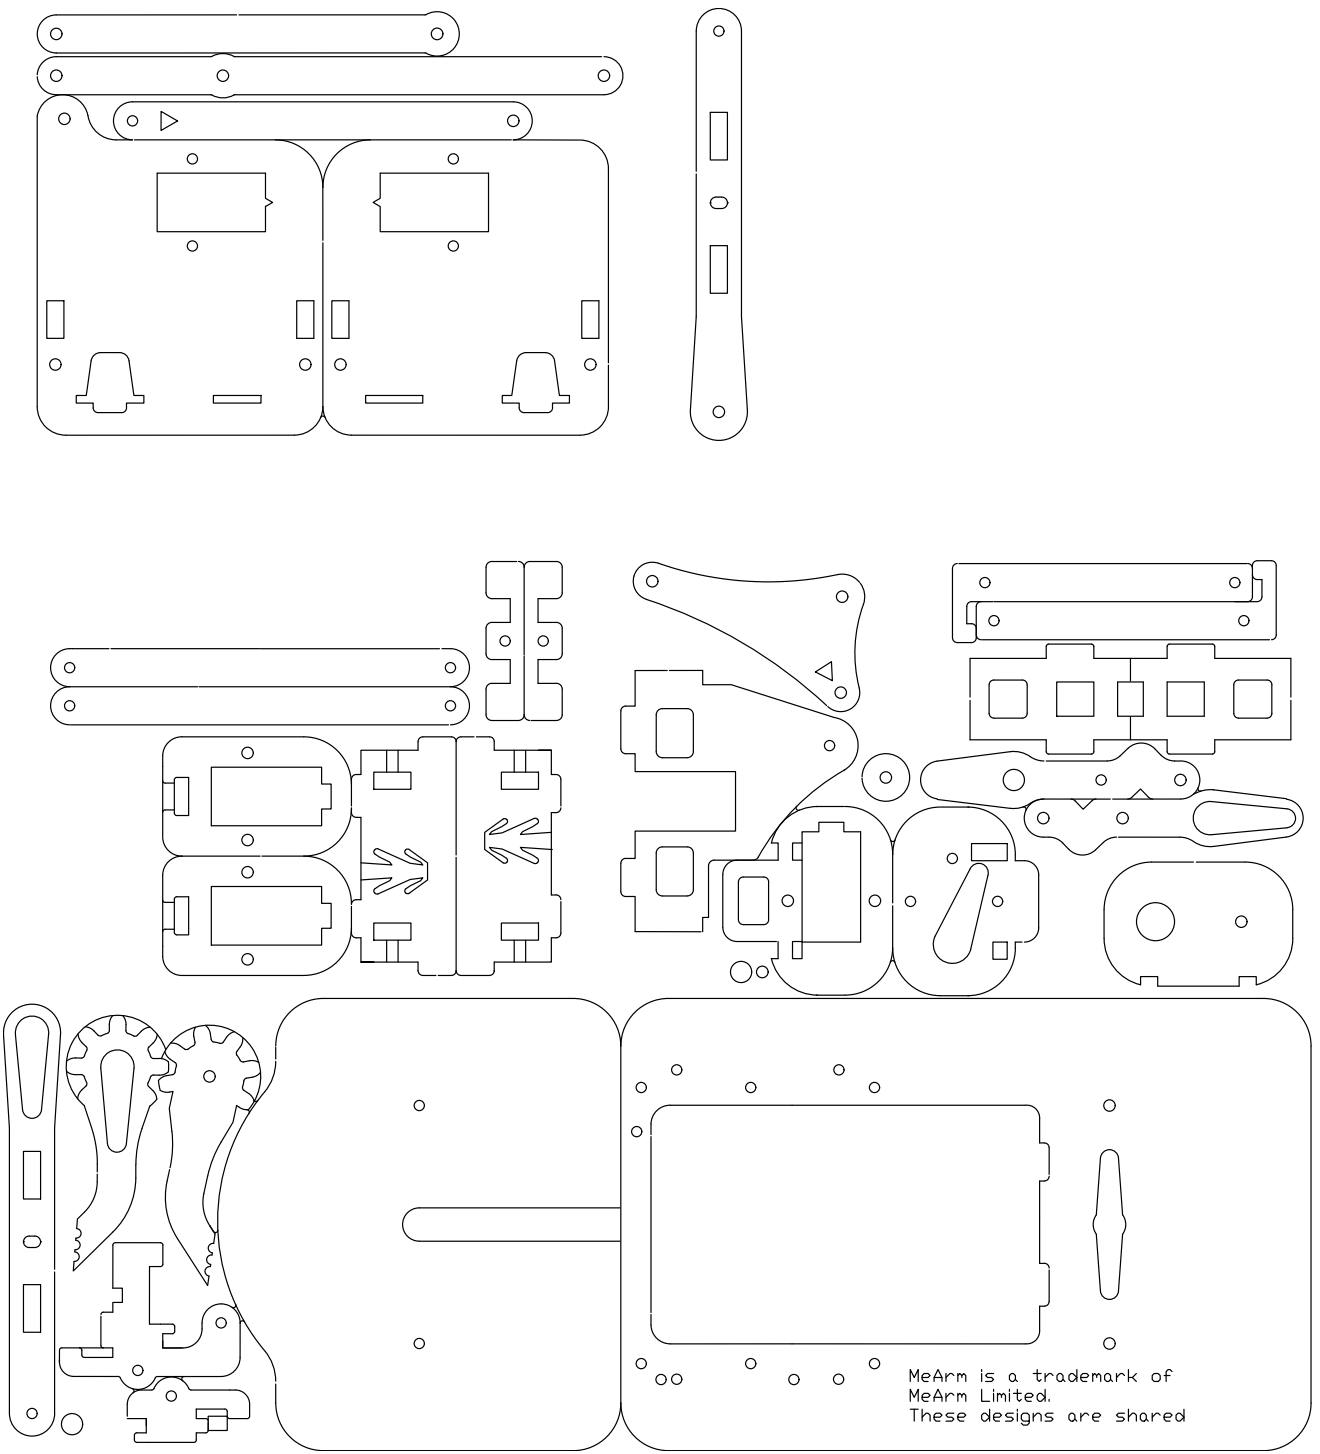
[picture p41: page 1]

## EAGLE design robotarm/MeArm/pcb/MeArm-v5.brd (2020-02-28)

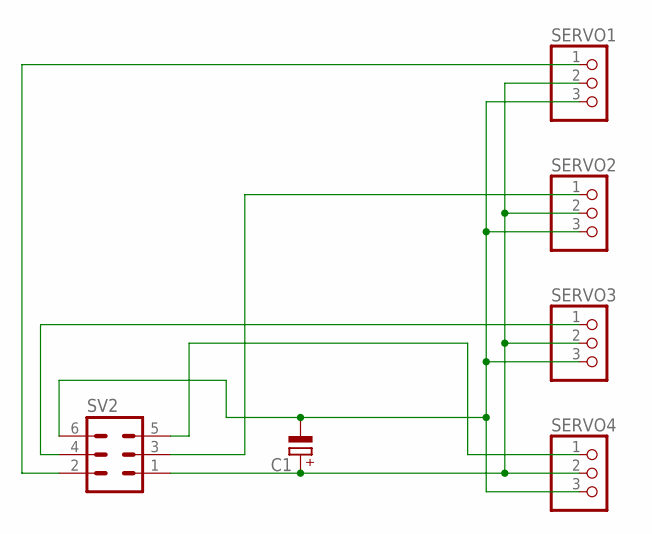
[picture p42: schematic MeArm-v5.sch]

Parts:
C1: CPOL-EUE2.5-6; E2,5-6
SERVO1, SERVO2, SERVO3, SERVO4: PINHD-1X3; 1X03
SV2: ML6

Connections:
unnamed: C1.+, SERVO1.2, SERVO2.2, SERVO3.2, SERVO4.2, SV2.1
unnamed: SERVO4.1, SV2.5
unnamed: SERVO2.1, SV2.3
unnamed: SERVO1.1, SV2.2
unnamed: C1.-, SERVO1.3, SERVO2.3, SERVO3.3, SERVO4.3, SV2.6
unnamed: SERVO3.1, SV2.4

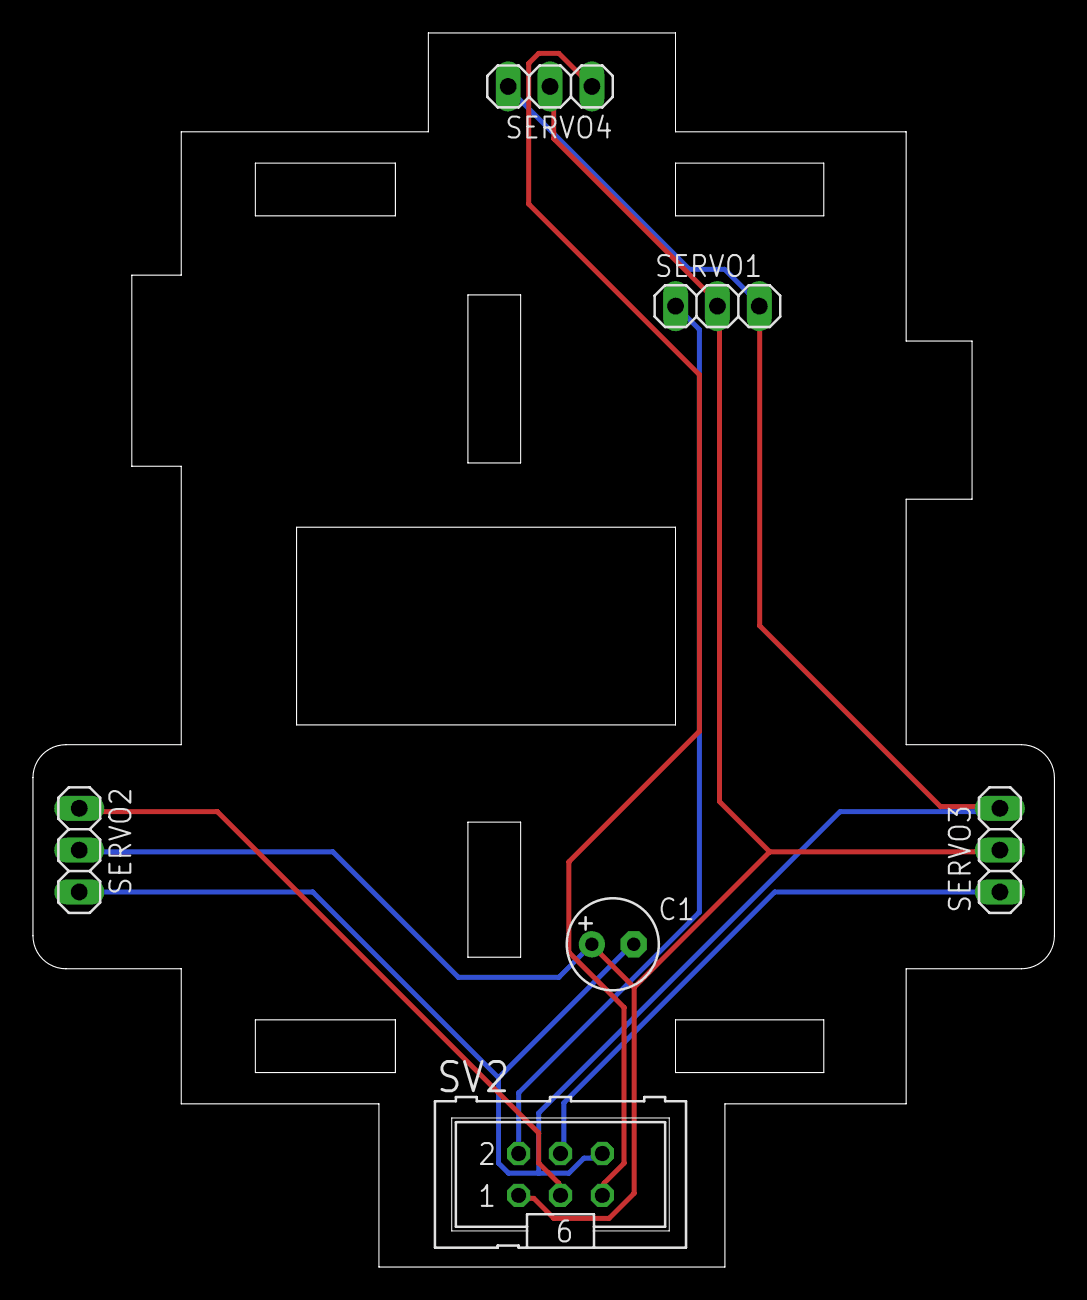
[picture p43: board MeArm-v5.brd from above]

Board: 2 copper layers, 62.0 x 74.9 mm, 6 parts (0 on the bottom side), 6 nets.

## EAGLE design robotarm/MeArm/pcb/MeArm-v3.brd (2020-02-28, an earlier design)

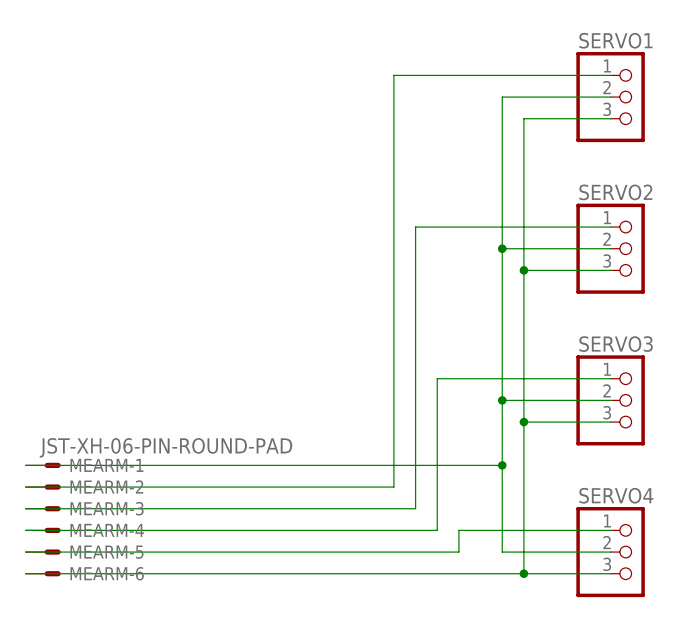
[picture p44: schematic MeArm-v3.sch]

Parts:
MEARM: JST-XH-06-PIN-ROUND-PAD; JST-XH-06-PACKAGE-ROUND-PAD
SERVO1, SERVO2, SERVO3, SERVO4: PINHD-1X3; 1X03

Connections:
unnamed: MEARM.1, SERVO1.2, SERVO2.2, SERVO3.2, SERVO4.2
unnamed: MEARM.5, SERVO4.1
unnamed: MEARM.4, SERVO3.1
unnamed: MEARM.2, SERVO1.1
unnamed: MEARM.3, SERVO2.1
unnamed: MEARM.6, SERVO1.3, SERVO2.3, SERVO3.3, SERVO4.3

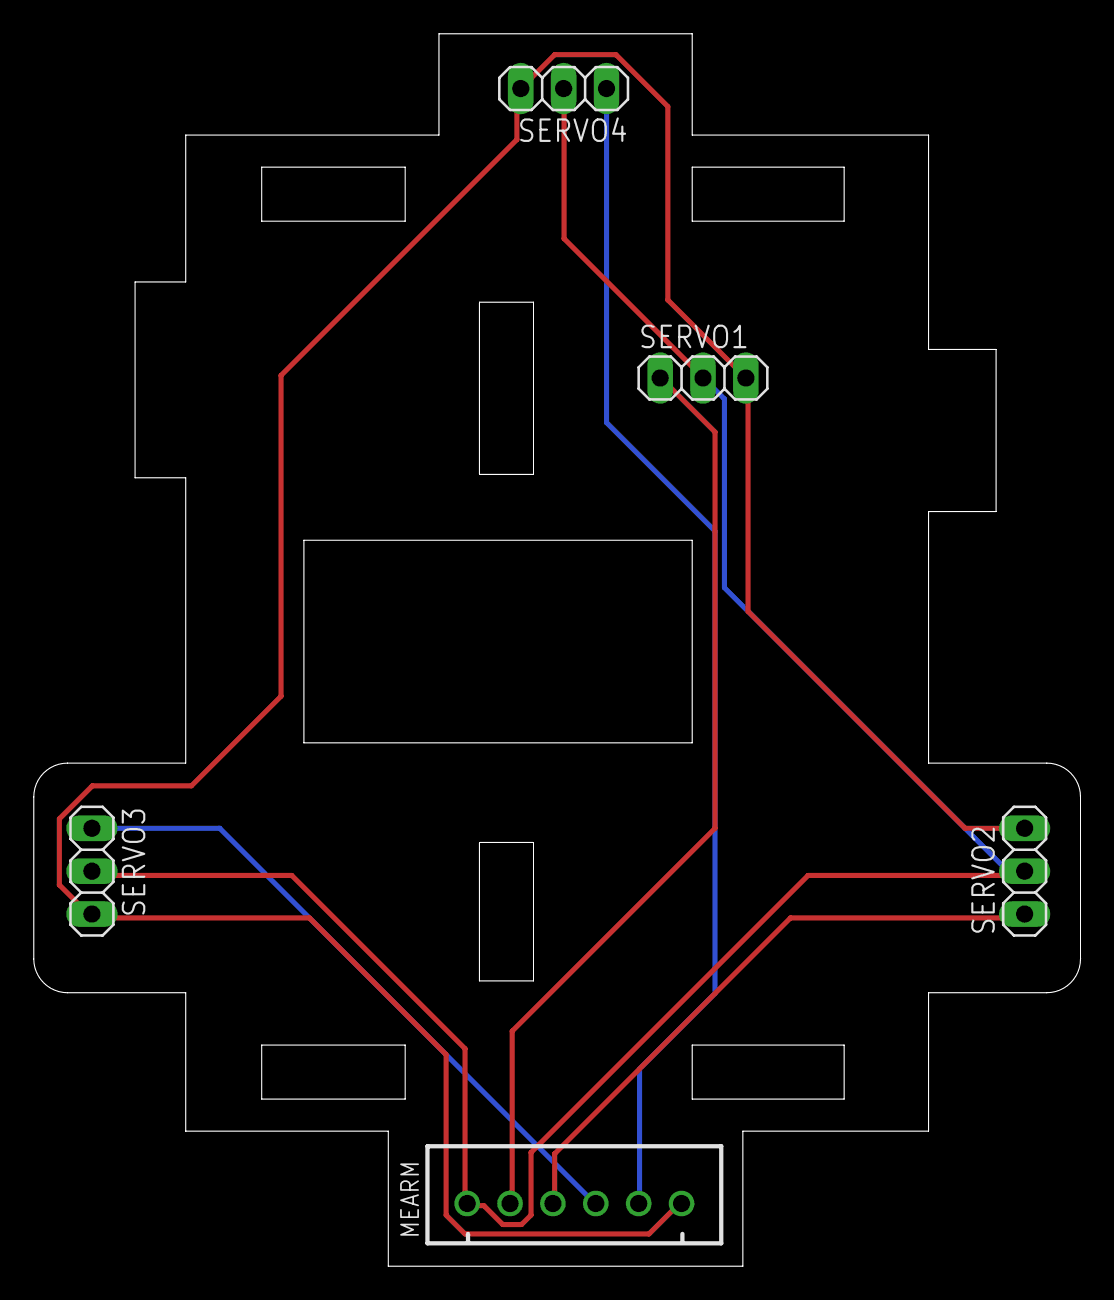
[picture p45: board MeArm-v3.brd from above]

Board: 2 copper layers, 62.0 x 73.0 mm, 5 parts (0 on the bottom side), 6 nets.

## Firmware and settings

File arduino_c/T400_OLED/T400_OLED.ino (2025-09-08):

/**
  @brief   Control ESP8266 Wifi Car with a smartphone in AP mode
  @author  Matthias Kreier
  @date    2024-03-13
*/

#include <ESP8266WiFi.h>
#include <ESP8266WebServer.h>
#include <U8g2lib.h>

const char *ssid = "Wificar24";
const char *password = "12345678";

IPAddress ip(192, 168, 42, 17);
IPAddress netmask(255, 255, 255, 0);
const int port = 8080; // Port
ESP8266WebServer server(port);

U8G2_SSD1306_128X64_NONAME_F_SW_I2C u8g2(U8G2_R0, 12, 14);
const char *dir = "X";

static const uint8_t pwm_A = 5 ;
static const uint8_t pwm_B = 4;
static const uint8_t dir_A = 0;
static const uint8_t dir_B = 2;

// Motor speed = [0-1024]
int motor_speed = 1024;

void setup() {
  Serial.begin(74880);
  Serial.println("\nWificar24");
  u8g2.begin();
  u8g2.setFont(u8g2_font_helvR10_tf);
  u8g2.drawStr(0,16,"SSID: T400_OLED");
  u8g2.drawStr(0,32,"PW: 12345678");
  u8g2.sendBuffer();  
  WiFi.mode(WIFI_AP);
  WiFi.softAPConfig(ip, ip, netmask);
  WiFi.softAP(ssid, password);

  pinMode(pwm_A, OUTPUT); // PMW A
  pinMode(pwm_B, OUTPUT); // PMW B
  pinMode(dir_A, OUTPUT); // DIR A
  pinMode(dir_B, OUTPUT); // DIR B

  server.on("/move", HTTP_GET, handleMoveRequest);
  server.onNotFound(handleNotFound);
  server.begin();
  u8g2.drawStr(0,48,"IP: 192.168.18.1");
  u8g2.drawStr(0,64,"Port: 8080");
  u8g2.sendBuffer();  
}

void loop() {
  server.handleClient();
}

void handleMoveRequest() {
  if (!server.hasArg("dir")) {
    server.send(404, "text / plain", "Move: undefined");
    return;
  }
  String direction = server.arg("dir");
  if (direction.equals("F")) {
    forward();
    server.send(200, "text / plain", "Move: forward");
    dir = "F";
  }
  else if (direction.equals("B")) {
    backward();
    server.send(200, "text / plain", "Move: backward");
    dir = "B";
  }
  else  if (direction.equals("S")) {
    stop_motors();
    server.send(200, "text / plain", "Move: stop");
    dir = "S";
  }
  else  if (direction.equals("L")) {
    turn_left();
    server.send(200, "text / plain", "Turn: Left");
    dir = "L";
  }
  else  if (direction.equals("R")) {
    turn_right();
    server.send(200, "text / plain", "Turn: Right");
    dir = "R";
  }
  else {
    server.send(404, "text / plain", "Move: undefined");
  }
  u8g2.setFont(u8g2_font_profont17_mf);
  u8g2.drawStr(110,64,dir);
  u8g2.sendBuffer();    
}

void handleNotFound() {
  server.send(404, "text / plain", "404: Not found");
}


void stop_motors() {
  analogWrite(pwm_A, 0);
  analogWrite(pwm_B, 0);
}

void backward() {
  analogWrite(pwm_A, motor_speed);
  analogWrite(pwm_B, motor_speed);
  digitalWrite(dir_A, LOW);
  digitalWrite(dir_B, HIGH);
}

void forward() {
  analogWrite(pwm_A, motor_speed);
  analogWrite(pwm_B, motor_speed);
  digitalWrite(dir_A, HIGH);
  digitalWrite(dir_B, LOW);
}

void turn_left() {
  analogWrite(pwm_A, motor_speed);
  analogWrite(pwm_B, motor_speed);
  digitalWrite(dir_A, HIGH);
  digitalWrite(dir_B, HIGH);
}

void turn_right() {
  analogWrite(pwm_A, motor_speed);
  analogWrite(pwm_B, motor_speed);
  digitalWrite(dir_A, LOW);
  digitalWrite(dir_B, LOW);
}

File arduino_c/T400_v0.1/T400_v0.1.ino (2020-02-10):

/**
  @file    wifi_car_esp8266_AP.ino
  @brief   Simple example of Wifi Car controlled by a web server in AP Mode. See also :
           http://www.instructables.com/id/A-very-cheap-ESP8266-WiFi-smart-car-controlled-by-/

           Example of commands to control the car :
           
           MOVE:
           - http://<YourIP>:<YourPort>/move?dir=F (Forward)
           - http://<YourIP>:<YourPort>/move?dir=B (Bacward)
           
           ACTION:
           - http://<YourIP>:<YourPort>/action?type=1 (Action 1)
           - http://<YourIP>:<YourPort>/action?type=1 (Action 2)


  @author  LACOUR Vincent
  @date    2019-10
*/

#include <ESP8266WiFi.h>
#include <ESP8266WebServer.h>
#include <Arduino.h>
#include <Wire.h>
#include <U8g2lib.h>

const char *ssid = "T401";
const char *password = "12345678";

IPAddress ip(192, 168, 4, 1);
IPAddress netmask(255, 255, 255, 0);
const int port = 8080; // Port
ESP8266WebServer server(port);

U8G2_SH1106_128X64_NONAME_F_SW_I2C u8g2(U8G2_R0, /* clock=*/ 12, /* data=*/ 14);
//U8G2_SSD1306_128X64_NONAME_F_SW_I2C u8g2(U8G2_R0, /* clock=*/ 12, /* data=*/ 14, /* reset=*/ U8X8_PIN_NONE);
String inputstring = "";
unsigned char* terminal[150]; // 8 lines with 25 characters
int input = 0;
int line = 0;
String direction_old;

static const uint8_t pwm_A = 5 ;
static const uint8_t pwm_B = 4;
static const uint8_t dir_A = 0;
static const uint8_t dir_B = 2;

// Motor speed = [0-1024]
int motor_speed = 1024;

void setup() {
  u8g2.begin();
  u8g2.firstPage();
  do {
    u8g2.setFont(u8g2_font_5x7_tf);
    u8g2.drawStr(0, 8,"T400 robot at AISVN ASA 3");
    u8g2.drawStr(0,16,"Creating WiFi network ...");
  } while (u8g2.nextPage() );
  WiFi.mode(WIFI_AP);
  WiFi.softAPConfig(ip, ip, netmask);
  WiFi.softAP(ssid, password);
  u8g2.firstPage();
  do {
    u8g2.setFont(u8g2_font_5x7_tf);
    u8g2.drawStr(0, 8,"T400 robot at AISVN ASA 3");
    u8g2.drawStr(0,16,"Creating WiFi network ...");
    u8g2.drawStr(0,24,"Please join: 'T401'");
    u8g2.drawStr(0,32,"Password: 12345678");
  } while (u8g2.nextPage() );

  pinMode(pwm_A, OUTPUT); // PMW A
  pinMode(pwm_B, OUTPUT); // PMW B
  pinMode(dir_A, OUTPUT); // DIR A
  pinMode(dir_B, OUTPUT); // DIR B

  server.on("/move", HTTP_GET, handleMoveRequest);
  server.on("/action", HTTP_GET, handleActionRequest);
  server.onNotFound(handleNotFound);
  server.begin();
}

void loop() {
  server.handleClient();
}

void handleMoveRequest() {
  if (!server.hasArg("dir")) {
    server.send(404, "text / plain", "Move: undefined");
    return;
  }
  String direction = server.arg("dir");
  //if( direction != direction_old) {
  //  direction_old = direction;
  //  inputline(direction);
  //}
  if (direction.equals("F")) {
    forward();
    server.send(200, "text / plain", "Move: forward");
  }
  else if (direction.equals("B")) {
    backward();
    server.send(200, "text / plain", "Move: backward");
  }
  else  if (direction.equals("S")) {
    stop_motors();
    server.send(200, "text / plain", "Move: stop");
  }
  else  if (direction.equals("L")) {
    turn_left();
    server.send(200, "text / plain", "Turn: Left");
  }
  else  if (direction.equals("R")) {
    turn_right();
    server.send(200, "text / plain", "Turn: Right");
  }
  else {
    server.send(404, "text / plain", "Move: undefined");
  }
}


void handleActionRequest() {
  if (!server.hasArg("type")) {
    server.send(404, "text / plain", "Action: undefined");
    return;
  }
  String type = server.arg("type");
  if (type.equals("1")) {
    // TODO : Action 1
    server.send(200, "text / plain", "Action 1"); // robot arm servo over i2c comes here ...
  }
  else if (type.equals("2")) {
    // TODO : Action 2
    server.send(200, "text / plain", "Action 2");
  }
  else if (type.equals("3")) {
    // TODO : Action 3
    server.send(200, "text / plain", "Action 3");
  }
  else if (type.equals("4")) {
    // TODO : Action 4
    server.send(200, "text / plain", "Action 4");
  }
  else if (type.equals("5")) {
    // TODO : Action 5
    server.send(200, "text / plain", "Action 5");
  }
  else if (type.equals("6")) {
    // TODO : Action 6
    server.send(200, "text / plain", "Action 6");
  }
  else if (type.equals("7")) {
    // TODO : Action 7
    server.send(200, "text / plain", "Action 7");
  }
  else if (type.equals("8")) {
    // TODO : Action 8
    server.send(200, "text / plain", "Action 8");
  }
  else {
    server.send(404, "text / plain", "Action: undefined");
  }
}

void handleNotFound() {
  server.send(404, "text / plain", "404: Not found");
}


void stop_motors() {
  analogWrite(pwm_A, 0);
  analogWrite(pwm_B, 0);
}

void backward() {
  analogWrite(pwm_A, motor_speed);
  analogWrite(pwm_B, motor_speed);
  digitalWrite(dir_A, LOW);
  digitalWrite(dir_B, HIGH);
}

void forward() {
  analogWrite(pwm_A, motor_speed);
  analogWrite(pwm_B, motor_speed);
  digitalWrite(dir_A, HIGH);
  digitalWrite(dir_B, LOW);
}

void turn_left() {
  analogWrite(pwm_A, motor_speed);
  analogWrite(pwm_B, motor_speed);
  digitalWrite(dir_A, HIGH);
  digitalWrite(dir_B, HIGH);
}

void turn_right() {
  analogWrite(pwm_A, motor_speed);
  analogWrite(pwm_B, motor_speed);
  digitalWrite(dir_A, LOW);
  digitalWrite(dir_B, LOW);
}

void inputline(const char* inputstring) {
  u8g2.firstPage();
  input++;
  if( line * 25 + 25 > input) {         // we need a new line
    if( input > 150 ) {                 // end of screen
      memcpy(terminal, terminal + 25, 125);
    }
    for(int i = 125; i < 150; i++) {
      *terminal[i] = '\n';
    }
    //strncpy(*terminal, inputstring, 150);
  } else {
    //*terminal[line] = (unsigned char*)inputstring;
  }
  do {
    u8g2.setFont(u8g2_font_5x7_tf);
    for(int i = 0; i < 8; i++) {
      const char* whatever = (const char *)*terminal[34];
      u8g2.drawStr(0, 8+8*i, whatever);
    }
  } while (u8g2.nextPage() );
}

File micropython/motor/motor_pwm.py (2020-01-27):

import machine
from machine import Pin, PWM
import time

pwm1 = PWM(Pin(5), freq=1000, duty=0)
pwm2 = PWM(Pin(4), freq=1000, duty=0)
M1 = machine.Pin(0, machine.Pin.OUT)
M2 = machine.Pin(2, machine.Pin.OUT)

M1.on() # forward
M2.on() # forward

print("Motor on")
speed = 10

while speed < 1030 :
  speed += 10
  time.sleep_ms(50)
  pwm1.duty(speed)
  pwm2.duty(speed)
  
print("Max speed")
  
while speed > 20:
  speed -= 10
  time.sleep_ms(50)
  pwm1.duty(speed)
  pwm2.duty(speed)

M1.off() # now backward
M2.off()

while speed < 1030 :
  speed += 10
  time.sleep_ms(50)
  pwm1.duty(speed)
  pwm2.duty(speed)
  
print("Max speed")
  
while speed > 20:
  speed -= 10
  time.sleep_ms(50)
  pwm1.duty(speed)
  pwm2.duty(speed)

pwm1.deinit()
pwm2.deinit()
print("Motor off")

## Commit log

2019-12-11 pin assignment
2019-12-11 code with reassigned i2c
2019-12-23 sample photos
2019-12-26 list of materials and code included
2019-12-30 updated materials list
2020-01-08 code and pin update
2020-01-13 extended robotarm
    [Gripper_1.stl, Gripper_2.stl, Gripper_4.stl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]
2020-01-16 updated pin assignment
2020-01-23 some noise every 200 ms
    [noise2.py]
2020-01-24 clean up
    [Gripper_1.stl, Gripper_2.stl, Gripper_4.stl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]
2020-01-29 upload pictures and dxf
    [MeArm1.1.dxf, MeArm1.1modified.dxf, MeArm3.0.dxf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]
2020-01-29 integraded MeArm 1.1 and 3.0
    [MeArm1.1modified.dwg, MeArm3.0modified.dwg]
2020-01-29 screws included and video updated
2020-02-10 design update
    [Base 9 simple v3.stl, Box 9 simple v2.stl]
2020-02-10 lasercut platform v0.1 2020-02-10
    [T400arm.dxf, T400arm_plain.dxf, T400platform.dxf]
2020-02-13 Create Box 9 simple v4.stl
    [Box 9 simple v4.stl]
2020-02-13 Create Base 9 simple v5.stl
    [Base 9 simple v5.stl]
2020-02-25 shape pcb pla
    [pcb_base v2.dwg, pcb_base v2.dxf, pcb_base v2.stl]
2020-02-26 reorganized 2020/02/27
    [MeArm1.1.dxf, MeArm1.1modified.dwg, MeArm1.1modified.dxf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]
2020-02-26 v3 dimensions fit 3d print
    [pcb_base.dxf, pcb_base_shrinked1.dxf]
2020-02-27 Create pcb_base v3.stl
    [pcb_base v3.stl]
2020-02-28 PCB in Eagle created
    [MeArm_v1.sch, pcb_base_v3.dxf, pcb_base_v4.dxf]
2020-02-28 gerber files v1
    [MeArm-v3.brd, MeArm-v3.sch]
2020-02-28 gerber detail files
    [copper_bottom.gbr, copper_top.gbr, drill_1_16.xln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]
2020-02-28 added capacitor, connector IDC 6P ML
    [MeArm-v5.brd, MeArm-v5.sch]
2020-02-28 images of PCB included
2020-03-04 refined design v2
    [Base9.stl, Box9.stl]
2020-07-09 included i2c connector assignment
2020-11-27 updated I2C connector definition
2020-12-11 i2c connector
2025-09-08 Updated T400_OLED.ino with u8g2 OLED driver

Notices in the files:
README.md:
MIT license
